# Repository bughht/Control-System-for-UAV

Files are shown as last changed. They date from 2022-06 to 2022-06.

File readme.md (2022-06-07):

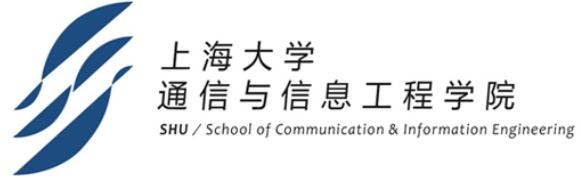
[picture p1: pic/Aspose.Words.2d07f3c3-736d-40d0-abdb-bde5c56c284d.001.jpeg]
scieyb


# 无人机自动投货系统

# **一、课题概述**

## **1.1 市场调研**

随着新科技被应用到如今的方方面面，企业和社会从中受益匪浅，当然，人们处理紧急情况的方式也变得多种多样。科技给我们带来了新的处理方式去处理紧急情况，为控制自然、人为等灾害的处置提供了新思路。随着美国联邦政府为无人机的运用出台的一些政策，无人机已经成为如今讨论的热点。和其他的科技一样，无人机的发展源自于军事应用。随着多轴无人机的发展，编程、稳定性、动力和价格方面都出现了改观，我们渐渐的也能制作出功能更复杂，功能更稳定的无人机。无人机处理紧急情况时拥有着令人关注的表现，给应急部门提供了一个新的思路来管理灾害的蔓延。

在过去，货物运送大多采用人工进行，这种模式无法高效快速地将所有小型货物准确的投掷到指定位置，对时间以及空间都有一定的限制，无法及时处理突发状况以及恶劣地形的跨越，也浪费人力资源。

2021年，中国民航局提出，在“十四五”期间，民航局将进一步扩大无人机物流配送试点范围。国家日益看重乡村振兴，大力发展乡村物流，无人机正成为推动乡村电商物流发展的重要利器。

结合现在科技的发展，我们需要找到让货物投掷便捷的方法来满足日益增长的需求。
## **1.2 需求分析**
（1）市场前景和应用价值

为了满足市场对无人机智能运输、准确投放上的需求，我们希望实现一个可便捷交互的基于树莓派和TM4C123GH6PM飞控板的无人机自动投弹系统。使用者可以通过拨码开关调整投掷物资的顺序，在飞机起飞之后，便可自动完成对周围场景的建模，寻找投放位置，躲避障碍并降落至投放区域，通过舵机自动投放，所有货物投放完成后自动返航等功能。以达到精准投放、自动返航的目的。

该项目的应用具有广泛性，可以用于各种无人投放场景，如偏远地区快递运送、极端地形物资投放等。且只需要一个激光雷达、一个摄像头、三个舵机、两块树莓派即可，性价比较高，可在多种地形上进行操作，通过拨码开关调整飞行程序，友好人性化，使用便捷。

（2）功能和核心技术

为了建立一个便捷、高效的无人机投放系统，我们主要实现三个功能：在指定位置投弹；路线规划和避障；稳定起飞和自动返航。

在指定位置投弹利用底部摄像头以及舵机，完成对无人机落地范围的控制。方便无人机及时地了解把握当前位置是否为投放位置；同时在画面上显示出投放位置的中心点和画面的中心点，方便程序实现期间的调试；根据计算可以得到无人机飞行方向，飞行距离。

路线规划和避障功能利用激光雷达对场景进行扫描的功能，获取障碍物所在的位置，由位置信息确定无人机飞行的路线。 

稳定起飞和自动返航功能，主要通过飞控板，控制螺旋桨调整飞行姿态和位置，并保持稳定。
## **1.3 实施过程**
（1）方案调整

①转接板PCB设计：计划初期我们原本打算用插针完成树莓派与舵机的连接，但因为连接不牢靠，更改为接线端子连接。由于我们的板子为异形板，设计空间较小，原定使用i2c等通信接口控制舵机等板载资源，但在实际过程中发现会导致树莓派性能降低，所以全部换为了普通GIOP口。

②树莓派与T265通信：为了压缩成本，我组打算用一块树莓派4b完成树莓派与T265等模块的通信。但在实验过程中发现，T265与树莓派4b的兼容性存在一定问题，连接不稳定，与老师讨论后认为是由树莓派USB硬件bug导致，因此，不得已再加入一块树莓派3b+，完成树莓派与T265的通信。

（2）具体进程

**A、实施阶段**

①初期学习、探索阶段

完成市场调研并进行分工，学习各自负责部分的相关内容，初步确定实施方案并进行试验测试可行性，了解树莓派与飞控板的通信方法。

第一周：确定课题，完成分工，完成市场调研。

第二周：详细计划完成，可行性报告完成。

第三周：树莓派环境配置，安装相应软件，学习相应知识。

第四周：学习3D打印，讨论无人机结构、投弹装置与电池仓设计。

②功能实现、制作阶段

完成PCB板以及3D打印部分，实现系统基础功能。

第三周：运用Altium Designer 完成PCB板设计。

第四周：PCB板送给厂家制作；树莓派与T265通信测试；

3D打印完成图纸设计；用3D打印得到的零件和实验室提供的零件尝试组装，试验无人机框架的结构。

第五周：PCB板完成焊接，LED灯模块、蜂鸣器模块调试；实现树莓派底部摄像头的部分功能；舵机功能测试；3D打印完成固定件。

第六周：实现舵机与树莓派的连接；实现树莓派程序对舵机的控制；树莓派激光雷达，T265的通信；3D打印外壳和支架等打印完成，底座设计完成；无人机各个模块的布局和应用设计。

第七周：3D打印基本完成；PCB板调试完成；各模块与树莓派数据包传输、舵机转动控制投放功能都已完成。

第八周：3D打印外壳优化完成；舵机供电改为5V电源供电；飞控板PID算法调试完成，可以实现起飞；飞控板与树莓派通信测试，经调整后可以正常工作；底部摄像头识别代码编写，基础功能可以实现。

③联合调试、完善阶段

飞控板与树莓派联合调试，可以实现基本功能。

第九、十周：各个模块代码整合；飞控板与树莓派通信；无人机联合调试，撰写结题报告。

2. **遇到的问题和解决方案**
1. 为了压缩成本，我组打算用一块树莓派4b完成树莓派与T265等模块的通信。但在实验过程中发现，T265与树莓派4b的通信存在问题，经常会断开连接，与老师讨论后认为是由树莓派USB口bug导致。再加入一块树莓派3b+后，问题解决。
1. 立创 EDA 绘制的 PCB 板文件不具有通用性，PCB 板重新使用 Altium Designer 设计。
1. 原来实验室中的机架无法完成项目要求，因此需要重新打印部分零件，以适配该任务。
1. 数字舵机与模拟舵机原理有些许不同，驱动代码有区别，需要修改，查阅资料调试后成功控制数字舵机。
1. 树莓派与无人机通信方面进展较缓慢，与组内成员项目互联通信时出现问题。检查后发现是树莓派转接板引脚虚焊导致，重新焊接后问题解决。
1. PCB 板排针与舵机杜邦线连接不牢固，同时舵机电源使用3.3V供电，电压不够，重新焊接改用5V 电源，取消杜邦线，连接就稳定了。
1. 飞机起飞时会向一侧偏离，飞控代码出现bug，查找修改后解决。

本小组成员在每次组会之后对存在的问题进行讨论，共同寻找解决方案，思路更加清晰、解决问题更加迅速。按照进度调整分工，让大家都有事可做，也提高了效率。

# **二、课题实施方案**
## **2.1 硬件总体方案**
小组成员根据本课题需完成的功能指标提出设计方案，并对可行性报告中最后确定的方案及课题实施中修改的方案进行说明，得出最后的最佳方案。

本项目的目标为制作一个自动无人机投弹系统，能够实时根据所处环境建立三维模型，根据三维模型规划路线，并完成投弹任务等。这需要我们设计并使用飞控板和树莓派开发板来进行数据分析和处理。基于以上需求，我们选择激光雷达作为我们测距建模的工具。讨论过后决定利用树莓派控制舵机进行投弹。使用TM4C123GH6PM飞控板控制飞行姿态。课题中树莓派需要实现较多功能，编写代码具有难度，在整个投弹系统中，需要较多的软件编写，实现课题目标。

本系统主要由四旋翼自主飞行器各部件构成。飞行器除机架、飞控板之外，主要包括激光雷达RPLIDAR A2和外接的树莓派及摄像头。下面分别论证整体设计方案中这几个模块的选择；首先，要完成定点投弹的功能，需要有较为准确的坐标系以保存所需遍历的点位信息。与用陀螺仪定位相比，T265所具有的精确坐标系更能体现出飞机的实时位置，也可以显著降低定位误差，故选用其坐标系统进行定位移动。其次，要实时判断飞行器下方是否为投弹区域，需要对无人机底部进行图像采集与图像处理。在本题中我们使用树莓派连接小型摄像头，采集底部中心一定范围之内的像素，并根据它们的色值判断其是否属于投弹区域。最后，在飞行到预定点位时，通过树莓派发出投弹指令。

本组采用的避障方式是使用SLAMTECA2激光雷达直接给出固定障碍物位置信息。因为激光雷达的精度更高，让无人机能够更好的检测当前处在的位置。故本组采用激光雷达对场景建模完成障碍物的识别。除此之外的基础功能包括舵机控制与 LED闪烁，蜂鸣器控制，都可以在树莓派上简便地完成。同时通过树莓派辅助处理飞行器速度信息。

基于总体设计方案，绘制的硬件原理框图如下图2.1。



图2.1  系统结构图
## **2.2 性能指标**
1. **飞行时间等：**起飞速度较快，垂直起飞，水平方向能按照预定路线稳定飞行。
1. **货物投掷位置与中心点距离：**底部摄像头能够准确的识别投放位置，并在相应的投放区域投放对应的货物，准确率较高。
1. **舵机控制：**舵机控制响应迅速，无多余抖动，水平旋转范围达 180°，能准确的放置货物仓中的货物并恢复原装。
1. **激光雷达：**能够通过激光雷达模块准确的建立模型，并且制定路线。
1. **稳定性：**在指定位置起飞后，能正常完成飞行认为并降落，偶尔会出现货物投放位置偏移。
## **2.3 开发平台**
无人机自动投弹系统开发采用的调试平台和软件编程语言。

1. PCB 板设计软件：Altium Designer。

`	`提供综合电子产品一体化开发所需的所有必须技术和功能。Altium Designer 在单一设计环境中集成板级和 FPGA 系统设计、基于 FPGA和分立处理器的嵌入式软件开发以及 PCB 版图设计、编辑和制造。并集成了现代设计数据管理功能,使得 Altium Designer 成为电子产品开发的完整解决方案——一个既满足当前，也满足未来开发需求的解决方案。

1. 3D 打印设计软件：Solidworks。

`	`Solidworks 是基于 Windows 平台的三维 CAD 设计和分析软件。其中 CAD 是计算机辅助设计（CAD-Computer Aided Design)是指运用计算机软件制作并模拟实物设计，展现新开发商品的外型、结构、彩色、质感等特色的过程。CAD 最早的应用是在汽车制造、航空航天以及大公司的电子工业生产中。之后随着CAD实现技术的演变和计算机价格的变化，其应用范围也逐渐变广，现广泛运用于平面印刷出版等诸多领域。

1. Keil MDK

`	`Keil MDK，也称MDK-ARM、Realview MDK、I-MDK、uVision4 等。Keil MDK是由三家[国内代理商]( )提供技术支持和相关服务。MDK-ARM软件为基于Cortex-M、Cortex-R4、ARM7、[ARM9处理器]( )设备提供了一个完整的开发环境。 MDK-ARM专为[微控制器](https://baike.baidu.com/item/%E5%BE%AE%E6%8E%A7%E5%88%B6%E5%99%A8/6688343)应用而设计，不仅易学易用，而且功能强大，能够满足大多数苛刻的嵌入式应用。

1. linux嵌入式操作系统

`	`Linux 内核最初只是由芬兰人林纳斯·托瓦兹（Linus Torvalds）在赫尔辛基大学上学时出于个人爱好而编写的。Linux 是一套免费使用和自由传播的类 Unix 操作系统，是一个基于 POSIX 和 UNIX 的多用户、多任务、支持多线程和多 CPU 的操作系统。Linux 能运行主要的 UNIX 工具软件、应用程序和网络协议。它支持 32 位和 64 位硬件。Linux 继承了 Unix 以网络为核心的设计思想，是一个性能稳定的多用户网络操作系统。
# **三、 课题实施详述**
## **3.1各模块设计**
1. PCB设计

`	`本项目需要用树莓派实现对舵机的控制，设计一块 PCB 板将树莓派 40 个引脚引出，针对需求对引脚进行合理的布局布线。PCB 板上设计了三个舵机插座、一个树莓派自身 5V电源插座、外部电源插座、蜂鸣器模块和 LED 模块，同时将剩余的引脚引到 PCB 板的上下端，以便备用，增加了 PCB 板的通用性。

①电路图设计思路

查阅树莓派引脚图资料，舵机的 PWM 波可由树莓派 GPIO 口直接输出，也可由特定的硬件 PWM 波 IO 口输出，将硬件 PWM 波 IO 口引出，（便可以测试两种方法，看哪个效果好就用哪一个）舵机还需要电源供电，考虑到用树莓派5V供电可能不够，便用转接板上的5V电源直接供电，并用MOS管驱动，树莓派控制的舵机在使用中能做到270°转动，但考虑到项目要求，一个舵机对软件编程会很困难，所以在 PCB 板上设计了三个舵机插座。引出树莓派自身 5V 供电电源，可以给一些小零件供电（比如风扇）。此外还设计了蜂鸣器模块和 LED 灯模块，蜂鸣器运用 MOS 管设计开关电路，GPIO 口输出高电平时，MOS 管导通，蜂鸣器响，反之，不响；LED 模块也是利用 GPIO 口输出PWM波控制MOS 管设计的开关电路，当输出高电平时，加上限流电阻，发光二极管便可以导通。

除了舵机、蜂鸣器等资源外，板子上还加入了一个5位拨码开关，降低编程同学的编程难度。

为了让树莓派更好的完成任务，我们在树莓派的CPU处加了小风扇进行主动散热，PCB设计的过程中，要避开风扇存在的区域。同时为了让转接板能稳定的安装在树莓派上，在板子四周留下过孔，便于对转接板固定。

电路原理图如下：



图 3.1 电路原理图

②各模块说明

LED 模块：GPIO 口输出高电平时，发光二极管导通，选择压降约为 0.7V 的发光二极管，MOS管压降约为0.3V，电源电压为 5V，发光二极管最大工作电流以 26mA 来计算，得限流电阻 R3=（5-0.7-0.3）/0.026 ≈150Ω，所以选择 150Ω 的电阻做为限流电阻，LED灯几乎达到最亮。

蜂鸣器模块：运用增强型NMOS管作开关，NMOS 的特性是Vgs大于一定的值就会导通，将 GPIO 输出口加到G极，当IO口输出高电平时大于限定值，MOS管导通，蜂鸣器发出声音。G极串联小电阻R1是为了减缓 Rds 从无穷大到 Rds(on)；防止电压突变 IO口与栅极电容形成 LC 震荡，串联电阻可以增大阻尼减小震荡效果；还能减小栅极充电峰值电流，一般取几欧姆到几十欧姆，这里选择 100Ω。栅极接地电阻 R2 是为了减少输入阻抗，减少对敏感信号的误动作，还有防静电的作用，阻值太大有可能起不到预期的效果，100kΩ 一般是比较可靠的。

舵机模块：GPIO 口输出高电平时，三极管导通，GPIO 口输出低电平时，三极管截止，因此在GPIO口输出PWM波时，MOS管源极处也能产生相应的PWM波，控制舵机旋转一定角度，然后复位。

插座模块：插座只需将需要的引脚连到同一个排针上即可。

最后将其余树莓派引脚引出即可。

③PCB 板的设计制作：

在画原理图之前，先将需要的所有元器件的封装找好，之后比较不容易出错，运用Altium Designer 画好原理图，打开封装管理器确保每个元器件封装尺寸，对应引脚正确，之后生成 PCB 设计图，进行布局和布线。在学习设计的过程中，要留意布局布线有各种规则（如电源线要比其他导线粗一些等），布局完成之前不要进行布线，否则，移动一个元件就会导致与它相连的线都必须重新连接。本项目的电路图较为简单，但板子面积较小，经过合理的布局之后正反两面的布线都没有出现交叉的情况。在布线完成后，对正反走线进行检查，添加丝印。在初步完成后，老师对 PCB 的设计提出了改进意见，首先连接外部电源的接线端子应该放在板子的边缘，方便插拔；其次 PCB 板与舵机的接口应该用接线端子，以提高连接的稳定性。最后是在板子上设计通孔（安装孔），方便以后系统增加功能需要叠加其他的板子，增加了 PCB 板的通用性。得到建议之后，再将 PCB 图进行修改布局布线，最后设置好各种规则，运行 DRC 检查，无误之后交给厂家生产。PCB 正反面图如下：



图 3.2 PCB正面



图 3.3 PCB 反面

拿到板子后，将元器件进行焊接，由于贴片电阻体积很小，焊接较为困难，在焊接的

过程中用万用表实时测试各个元件是否虚焊。在焊好第一个之后，联合舵机调试有问题，

于是重新焊接了一块板子，测试无误，PCB 板部分完成。

（2）舵机控制

树莓派 PWM 波输出端口控制舵机转动，用 GPIO23、24、25（实际地址）口进行软 PWM 波输出。运用库中的 PWM 函数控制数字舵机。用5V 电源供电。

舵机型号初选定为 TBSN-K15，通过树莓派 GPIO12 引脚输出硬件生成 PWM 波控角度。舵机的控制信号为周期是 20ms 的脉宽调制（PWM）信号，其中脉冲宽度从 0.5ms-2.5ms，相对应舵盘的位置为 0－180 度，呈线性变化，一一对应。也就是说，给它提供一定的脉宽，它的输出轴就会保持在一个相对应的角度上，无论外界转矩怎样改变，直到给它提供一个另外宽度的脉冲信号，它才会改变输出角度到新的对应的位置上。舵机内部有一个基准电路，产生周期 20ms，宽度 1.5ms 的基准信号，有一个比较器，将外加信号与基准信号相比较，判断出方向和大小，从而产生电机的转动信号。

舵机的控制电路板接受来自信号线的控制信号，控制电机转动，电机带动一系列齿轮组，减速后传动至输出舵盘。舵机的输出轴和位置反馈电位计是相连的，舵盘转动的同时，带动位置反馈电位计，电位计将输出一个电压信号到控制电路板，进行反馈，然后控制电路板根据所在位置决定电机的转动方向和速度，从而达到目标停止。

根据理论，只要输出占空比为 2.5%到 12.5%的 PWM 波信号，就可以控制舵机从0-180°旋转，但经过校准后，发现该数字舵机 0°是对应输出 5%的 PWM 波信号，180°对应 12.5%的 PWM 波信号，所以控制占空比在 5%-12.5%之间变化，转动角度也跟着线性变化。



图 3.4 舵机基本参数表和外观图

（3）树莓派

树莓派3B+系统结构图如下图6。

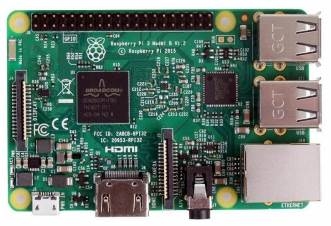
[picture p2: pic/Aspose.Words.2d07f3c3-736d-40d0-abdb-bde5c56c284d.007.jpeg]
src=http%3A%2F%2Fwww


图3.5树莓派系统结构图

树莓派3B+参数如下：

CPU型号：Broadcom BCM2837 芯片组，四核Cortex-A53（ARM v8）64位SoC @ 1.5GHz

内存： 8GB 

无线网卡： 2.4 GHz和5.0 GHz IEEE 802.11ac无线，蓝牙4.2，BLE

有线网卡： 1 x 10/100 以太网端口

USB接口： 4个USB 2.0端口

GPIO引脚： Raspberry Pi标准40针GPIO接头连接器（与以前的板完全向后兼容）

显示器接口： 1个micro-HDMI端口（最多支持4kp60）

DSI屏幕： 2通道MIPI DSI显示端口

CSI摄像头： 2通道MIPI CSI摄像机端口

视频输出： 4针立体声音频和复合视频端口

H.265（4kp60解码），H264（1080p60解码，1080p30编码）

OpenGL ES 3.0图形

内存卡插槽： Micro-SD卡插槽，用于加载操作系统和数据存储

电源输入： 通过USB-C连接器5V DC（最小3A \*）

通过GPIO接头提供5V DC（最小3A \*）

POE供电： 启用以太网供电（PoE）（需要单独的PoE HAT）

工作温度： 0 – 50摄氏度环境

4. 飞控板

如下图7所示。

PKRUR(A\_IE2F%Z91N8\_SANF 8SW2WH%OREE1HEN9[1WRD]4

图3.6 TM4C123GH6PM 飞控板

采用高性能的 TM4C123GH6PM 芯片，主频为 80MHz。电池电压经电调降压后输入飞控板，一路 3.3V 稳压负责供应板子上的核心芯片，另一路负责所有的外部设备。配备 2 路舵机接口，可以由飞控直接控制舵机转动。飞控板上从单片机引出了 1 路 I2C 接口和 4 路Uart 接口，具有丰富的扩展性。设计时为了使设备工作更加稳定，选用了 4 枚大容量钽电容，以应对电流陡升的情况，确保飞行稳定。

4. 激光雷达

RPLIDAR A2 由 SLAMTEC 公司开发的新一代低成本二维[激光](_blank)雷达(LIDAR)，它具有每秒高达 8000 次的高速激光测距采样能力。并配备了 SLAMTEC 独有的光磁融合(OPTMAG)专利技术，克服了传统激光雷达的寿命限制，可长时间可靠的稳定运行。

RPLIDAR A2 可以实现在二维平面的 12米半径范围内进行 360 度全方位的激光测距扫描，并产生所在空间的平面点云地图信息。这些云地图信息可用于地图测绘、机器人定位导航、物体/环境建模等实际应用中。本项目利用该雷达在飞行场地建立云图。

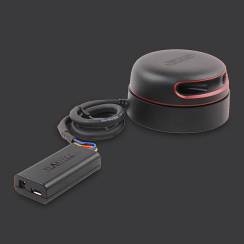
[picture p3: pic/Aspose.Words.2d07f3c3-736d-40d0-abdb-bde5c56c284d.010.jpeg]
o4YBAF3Of8WAKZXMAAC4QOJQnk8889


图3.7  RPLIDAR A2模块

（6）3D打印

`    `本产品使用SolidWork进行无人机的3D打印。打印的部件包括两块底板、树莓

派外挂板、三个投弹装置与八个机脚固定支架。

`    `底座板1提供与三个投弹装置的螺丝孔，提供超声底座连接的螺丝孔，同时

还提供与第二块底座板连接的减震球孔。如图9



图3.8 底座板

`    `第二块底板上有能够与第一块底座板连接的减震球孔，以及底部摄像头底座连接

的螺丝孔。如图10



图3.9 底座板2

`    `超声底座能够固定超声雷达，同时能够连接至底座板1。如图11



图3.10 超声底座

底部摄像头底座能够固定底部摄像头，同时能够连接至底座板2。如图12



图3.11 底部摄像头底座

投弹装置能够利用舵机装置来实现圆柱体的投放，固定在底座板1上。如图13



图3.12 投弹装置

树莓派外挂板提供树莓派以及树莓派扩展板的固定，侧板固定在无人机的底座

上。如图14



图3.13 树莓派外挂板

`    `机脚固定支架用于固定四个撑脚，使起飞与降落更加稳定。如图15



图3.14 机脚固定支架

`     `飞控底座上放置飞控模块，飞控底座通过减震球连接至中层板。如图16



图3.15 飞控底座

中层板提供与上层板的连接以及飞控底座的连接，最外侧提供与飞机主体的连

接。如图17



图3.16 中层板

`        `上层板提供激光雷达的支撑以及T260的支撑。如图18



图3.17 上层板

`    `飞机展示：

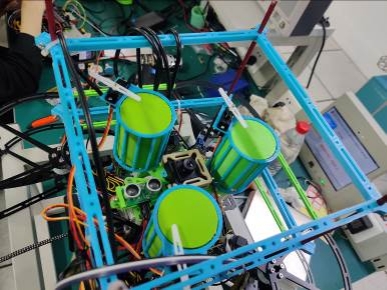
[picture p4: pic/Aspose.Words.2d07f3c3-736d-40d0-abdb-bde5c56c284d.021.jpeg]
DA1A3113C92C068D3B61A7594309E88E


图3.18 飞机底部

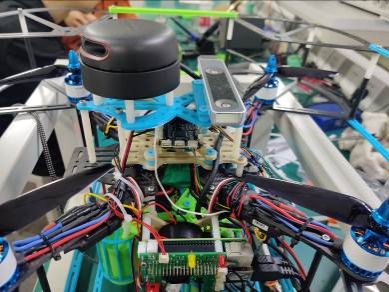
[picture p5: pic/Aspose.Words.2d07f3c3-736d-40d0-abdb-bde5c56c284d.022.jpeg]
288976D5343EC8E4D051DC27644402A7


图3.19 飞机顶部

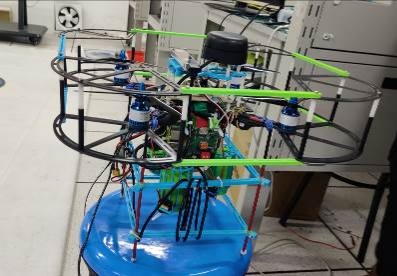
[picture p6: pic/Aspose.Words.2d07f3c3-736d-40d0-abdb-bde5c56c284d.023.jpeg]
AB2DF2DDD4166C45FAF4F75924F756BD


图3.20 飞机整体
## **3.2软件编程**
本飞机的基础框架基于408实验室的飞机，其基本的飞行功能早已成熟，因此在本报告中不再赘述。本章节后部分介绍的主要为本组在飞控上的改变以及为完成 本任务而新增的程序部分。

**（1）树莓派4b**

**①底部摄像头**

为了实现精准降落投货，我组在飞机的下部增加了一个对地摄像头。该摄像头和树莓派4b相连，主要用于抓取地面降落点中心的具体位置信息，再将信息通过自定义的编码方式，经由UART口传输到飞控程序中，辅助飞机落地。

具体实现过程：通过树莓派打开摄像头后，获取到其中的每帧图片信息，对得到的图片进行缩放、腐蚀以及膨胀等操作，得到一张便于处理的图片。由于地面降落区域中有大部分区域为红色，所以本组决定通过控制颜色阈值来找降落部分的中心。在得到对应颜色的RGB阈值之后，对处理过的图像进行mask处理，可以得到降落区域的范围图，再通过边缘检测，找到一个恰好框住降落区域最小的方形，该方形的中心即可粗略认为是降落区域的中心。流程图以及具体的算法流程如下图所示：



图3.21 底部摄像头算法流程

其中加入的降采样是为了减轻树莓派的计算负担，mask后的结构更易找到目标色块，根据边缘找中心点也可以稍微减轻计算量。进行以上优化后，树莓派可以实时处理视频图像。

为了改善程序对物理设备的状态控制，以面向对象的思想创建了一个Cam类。具体代码见附录。

**②激光雷达**

该任务中有避障这一环节，为解决这一问题，我组在飞机的最上方新增了一个激光雷达。该雷达也是和树莓派4b相连。在树莓派上安装好相关软件的驱动之后，就可以获得飞机四周的点图。之后确定滤除飞行区域外部的点，得到的就是飞行区域内的障碍物的点图，再根据极坐标的转换，就可以得到飞机内部坐标系下（即T265坐标系）障碍物的坐标。

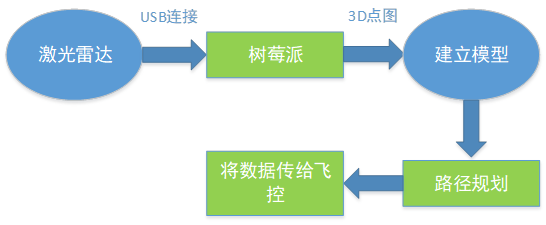
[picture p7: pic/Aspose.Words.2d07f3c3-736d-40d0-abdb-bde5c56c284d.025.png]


图3.22 激光雷达算法流程

路径规划：就是让检测到障碍物之后，以障碍物为圆心做圆，当飞机进入到以障碍物为圆心，一定范围内为半径的圆的边缘处时，就给予无人机一个对应圆环的切线的速度，使之能够走一个圆形避开障碍物。具体实现时，需要积累开始避障时圆形边缘的点和圆心的角度，到后面对应角度停止。示意图如下。

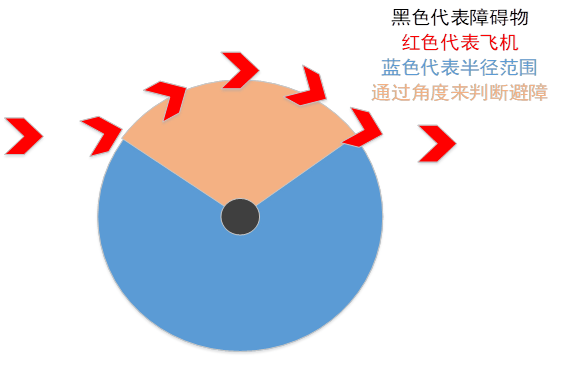
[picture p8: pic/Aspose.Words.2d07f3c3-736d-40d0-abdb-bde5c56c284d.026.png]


图3.23 飞机避障示意图

**③舵机控制**

当飞机成功降落到投货区域后，需要控制舵机将货物投下，为实现这一目标，我们将舵机和树莓派相连接，当树莓派接收到飞机发送过来的投货信号时，在对应的引脚上输出固定的PWM信号，控制舵机放下货物并且恢复原位。

为了方便调试，我们还在树莓派上加入了单独的蜂鸣器和LED灯（独立于飞控上的设备，方便通信方面的调试）。下为树莓派上引脚和接出来的硬件的对应图：

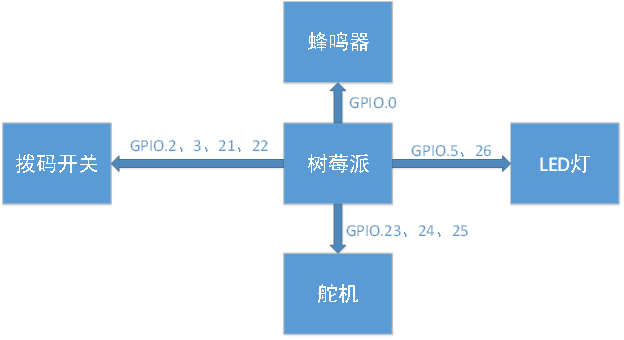
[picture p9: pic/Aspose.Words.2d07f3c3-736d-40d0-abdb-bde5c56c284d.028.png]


图3.24 树莓派与转接板连接引脚

由于这三个外接在树莓派上的设备都是用PWM驱动的，只是其中的脉宽以及占空比有一定打差距，下框图展示了树莓派如何在对应引脚上输出PWM信号。



图3.25 PWM波的输出

本次项目中，舵机、LED以及蜂鸣器的控制都是基于上图，但是为了用正确的PWM信号控制上述设备，中间所设计的参数有所不同。

驱动舵机需要不停地切换占空比，因此在程序设计时，我们用两个循环，设置两个渐变的占空比，实现自动打开舵机投货，并且在投货结束后自动关闭舱门。

LED灯和蜂鸣器的控制则轻松许多，只需要按照闪烁（鸣叫）的需求设置占空比即可。

1. 通信部分

原本我组想沿用之前的MAVLINK传输，但是由于其传输的性能在本飞机上并不佳，并且由于是祖传的代码，其中有一些问题难以通过代码简单解决，于是本组决定把部分通信协议改为基于UART口的hht协议。

重写的部分主要是树莓派4b和飞控之间的通信协议，我们将发送的数字压缩放入到一个数组中，通过UART口对进行二者之间的通信。该通信协议十分的简陋，仅有部分简单的对其和校验，但是经实验证明，已经可以满足我们的需求。前部分摄像头处理之后获得的图像信息、激光雷达处理后的障碍物的位置信息以及飞控给树莓派4b的投货信号都是通过这个协议进行传信的。

具体协议示意图如下：



图3.26 树莓派与飞控通信协议

1. 飞控部分的改进

为了进一步加快飞机飞行的速度，我们对飞控的部分代码进行了改写。

其一：我们对起飞进行了一定的优化，在飞机起飞之前加入了一段T265预载时间，这也可以大大减小T265在开机时出问题的可能性，再加上软件上的主动清零、校准，使得起飞时坐标系更加准确，有利于之后的定位。

其二：我们对基础的飞行代码也进行了一定的优化。之前的飞行是直接设置一个速度，用恒定速度进行飞行，最后用T265的数据进行校准，判断是否到位置。这样虽然可以完成飞行任务，但是飞行速度过慢，因此我们选择用速度控制实现直线飞行。与之前的恒定速度不同，新的控制代码用距离来控制速度，这样可以显著增加飞行速度，而且可以更好地找到重点。

其三：我们还将摄像头数据融入到飞控中，可以实现在直线上任意目标点停止（目标点有特殊标志）。

最后，我们还对降落进行了优化，为了节省时间，我们把原来的垂直下落改成倾斜下落，这样也能大幅度减少飞行时间，可以用更短的时间完成任务。
# **四、 系统测试及结果分析**
## **4.1 系统测试**
本项目的系统应用在 T408 实验室。烧录好程序后，用一个开关控制无人机开机，为实验室内师生提供极大便利，实物系统如下图。

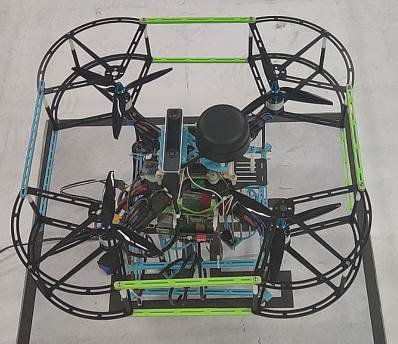
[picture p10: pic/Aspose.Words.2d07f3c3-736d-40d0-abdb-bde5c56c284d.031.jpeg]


图4.1 实物系统

在安装好电池并确认各个模块连接正常之后，便可开始本次测试。基于本项目的实质内容，将其主要分为三大模块：飞行寻路，躲避障碍和货物投掷。

1. 飞行寻路功能测试

①起飞稳定阶段

在起飞之前要先经过一段时间的准备和等待蜂鸣器鸣叫后，说明树莓派已经启动完备，准备起飞。如图4.2所示。

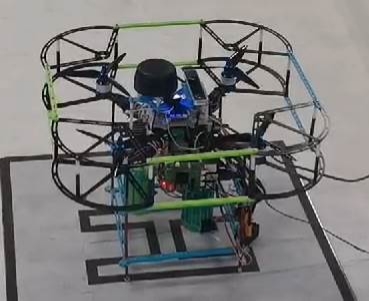
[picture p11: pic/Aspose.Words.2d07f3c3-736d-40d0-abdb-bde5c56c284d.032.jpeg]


图4.2 准备起飞阶段

起飞时，通过T265传回的数据调整飞行姿态，使飞机稳定起飞。定高飞行时如下图所示。

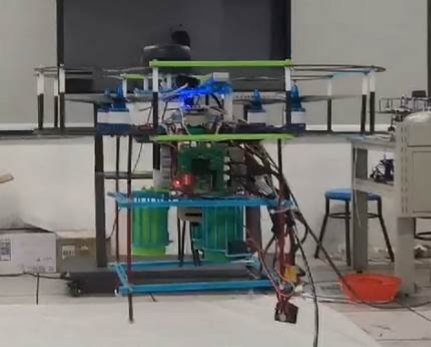
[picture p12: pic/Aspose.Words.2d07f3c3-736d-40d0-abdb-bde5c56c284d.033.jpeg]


图4.3 飞行定高阶段

起飞所花费时间如下表：

表4.1 飞行时间统计

|起飞测试次数|起飞消耗时间|
| :- | - |
|第一次测试|3.32s|
|第二次测试|3.45s|
|第三次测试|3.28s|
成功起飞后，向前飞行寻找投掷位置，并降落。

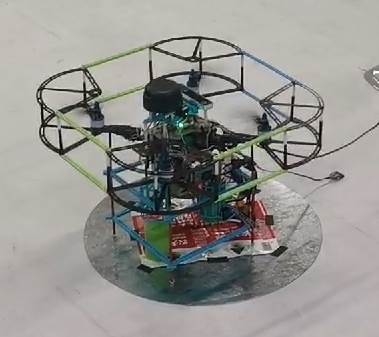
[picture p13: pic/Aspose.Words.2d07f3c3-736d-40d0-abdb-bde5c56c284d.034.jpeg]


图4.4	第一个点位降落位置

在找到第一个点位并降落后，树莓派控制舵机进行投弹，完成后再次起飞，向右侧飞行寻找第二个投弹位置。重复这一步骤，寻找第三个点位。

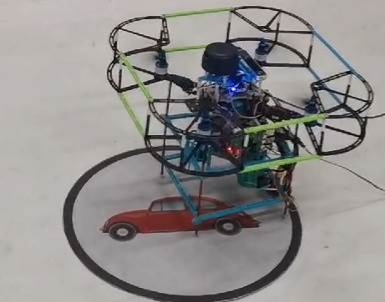
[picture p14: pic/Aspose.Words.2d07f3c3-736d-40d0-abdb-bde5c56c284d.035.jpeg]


图4.5	第二个点位降落位置

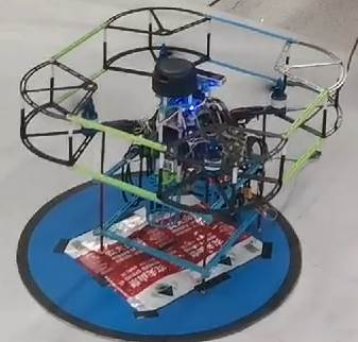
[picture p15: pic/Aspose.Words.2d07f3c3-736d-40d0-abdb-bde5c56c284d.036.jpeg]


图4.6	第三个点位降落位置

寻找完全部点位后，飞回起飞位置，并降落。降落位置如图4.7 所示。

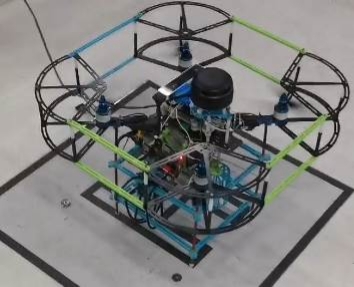
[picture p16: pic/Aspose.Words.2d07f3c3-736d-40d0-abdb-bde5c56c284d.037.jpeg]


图4.7 飞回起点的降落位置

1. 躲避障碍功能测试

在飞行的路上会人为设置障碍物，树莓派通过激光雷达建立返回的数据建立模型，并躲避障碍物，绕杆飞行躲避障碍时图片如下。

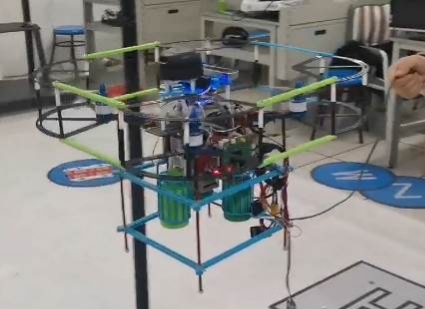
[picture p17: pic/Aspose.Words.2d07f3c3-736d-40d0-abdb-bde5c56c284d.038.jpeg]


图4.8 无人机避障

（3）货物投掷功能测试

当飞机成功降落到投货区域后，需要控制舵机将货物投下，为实现这一目标，我们将舵机和树莓派相连接，当树莓派接收到飞机发送过来的投货信号时，在对应的引脚上输出固定的PWM信号，控制舵机放下货物并且恢复原位。投掷位置如下图。



图4.9 第一个货物投掷位置



图4.10 第二个货物投掷位置

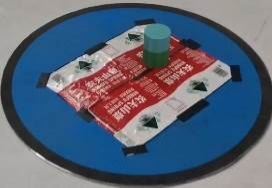
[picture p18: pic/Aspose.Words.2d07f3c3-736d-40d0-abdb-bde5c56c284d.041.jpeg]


图4.11 第三个货物投掷位置

调试飞控时有用到JLINK，以及串口助手。JLINK主要用于烧录飞控程序，在必要的时候还可以用它来调试部分飞控程序。串口助手则主要用于调试串口通信。等飞机起飞之后，我们就只能通过WiFi连接观察树莓派上的数据情况。

上面提到的所有新加的模块，我们都通过正确的手段进行测试过，保证每一个模块都可以完美运行之后才上电进行飞行测试。

最终在我们不懈的调试下，飞机可以成功完成全部的飞行任务。
## **4.2 结果分析**
以表格形式给出系统测试结果。

表4-2  系统测试结果

|**系统功能**|**设计结果**|**与设计指标间的偏差与分析**|
| :-: | :-: | - |
|**飞机起飞与寻路**|能够稳定起飞并且定高飞行，起飞时间较短，定高飞行时有微量偏移，可以忽略不计|无偏差，起飞流畅稳定。|
|**树莓派与飞控通信**|未起飞时通过串口测试，数据收发正常，起飞后也能正常通信，传输树莓派处理过的信息给飞控。|无偏差，能够根据数据及时调整飞行姿态。|
|**底部摄像头图像处理**|通过树莓派打开摄像头后，获取到其中的每帧图片信息，对得到的图片进行缩放、腐蚀以及膨胀等操作，得到一张便于处理的图片。再利用色彩阈值识别投弹位置，进行投掷。|有略微偏差，投掷位置与中心点相距5cm左右。|
|**激光雷达得到3D模型并规划路线避障**|在树莓派上安装好相关软件的驱动之后，就可以获得飞机四周的点图。之后确定滤除飞行区域外部的点，得到的就是飞行区域内的障碍物的点图，再根据极坐标的转换，就可以得到飞机内部坐标系下（即T265坐标系）障碍物的坐标。|无偏差，能够识别并躲避场地上的障碍。|
|**树莓派控制舵机投掷货物**|基于树莓派输出的 PWM 波实现了舵机的控制，初始化时 90 度，步进为 2度，可进行 0～180 以内任意角度的步进调整和定位调整。|无偏差，无人机可根据自身需求调整舵机释放货物|

# **五、总结与展望**
经过一个学期的努力，我们小组完成了无人机自动投弹系统这个项目。从项目初期的懵懂学习，到中期方案调整，最后到后期的功能完善，每一步我们都付出了很多心血。项目初期，我们进行了市场调研，了解到市场上各种无人机自动投弹系统的优缺点以及考虑到本身能力后，制定好了设计方案，最后得以实现系统基本功能。本课题可以实现对周围场景的建模，寻找投放位置，躲避障碍并降落至投放区域，通过舵机自动投放，所有货物投放完成后自动返航等功能。

通过这个项目，小组成员对 3D 打印、PCB 板设计、树莓派和飞控板都有了更多的了解，每个人对于自己的分内的工作都很上心，熟练掌握相关知识。在开发过程中，我们也遇到了许多问题，但我们每周都会进行小组研讨，对上周完成了任务做一个总结并讨论存在的问题，最终想出最佳的解决方案并尝试，这种探讨与思考不仅提高了我们解决问题的能力，还使得小组的凝聚力愈加深厚。

这个系统还有很大的改进空间，比如飞行器的结构并不完美，硬件资源潜力没有全部发挥等等，之后如果有机会，我们还会在系统上进行改进，对各种性能进行优化，使它成为一个更加完善和稳定的系统。
# **参考文献**
[1]Altium Designer2019四层板智能车PCB设计视频教程 https://b23.tv/2pwwB7

[2]赵宏、包广斌、马栋林.Python 网络编程(Linux)[M].清华大学出版社:北京,2018:16.

[3]陈鹏,李子卓,李陈龙,宋昊铭,吴心雨,迟英姿.物流无人机PID控制研究[J].无线互联科技,2021,18(23):112-113.

[4]芦竹茂,武娜,赵亚宁,白洋,韩钰,高海跃.基于激光雷达的无人机在杆塔附近的定位研究[J].激光与光电子学进展,2022,59(04):28-36.

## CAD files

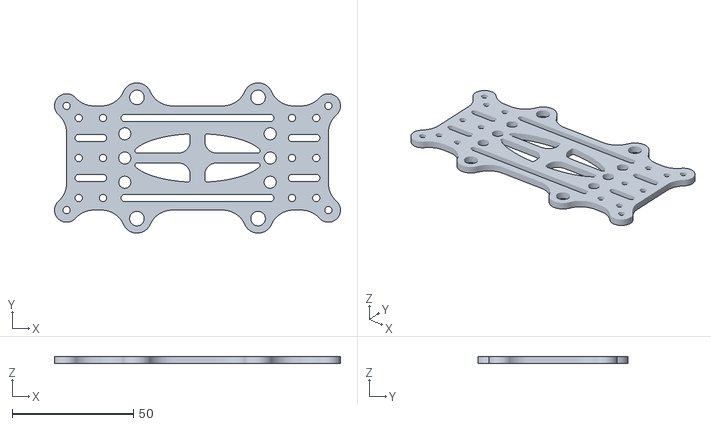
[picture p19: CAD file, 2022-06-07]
3D_Model/UP_BOTTOM v4.stl
118.0 x 62.0 x 3.00

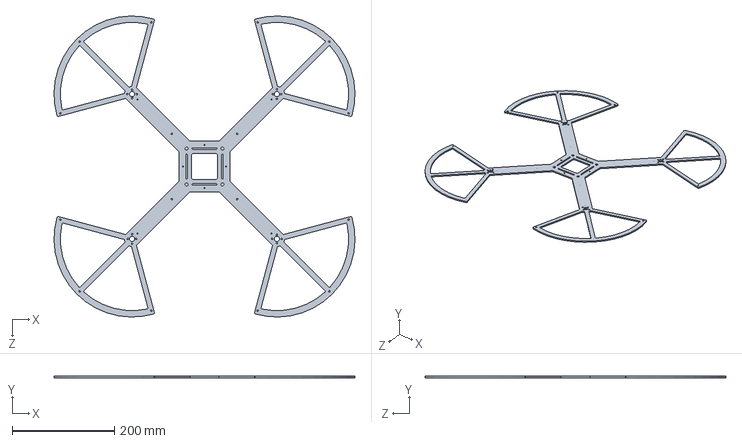
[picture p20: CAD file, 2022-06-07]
PCB/转接板 (3)/转接板/机架1.SLDPRT
587.8 x 3.00 x 587.8 mm

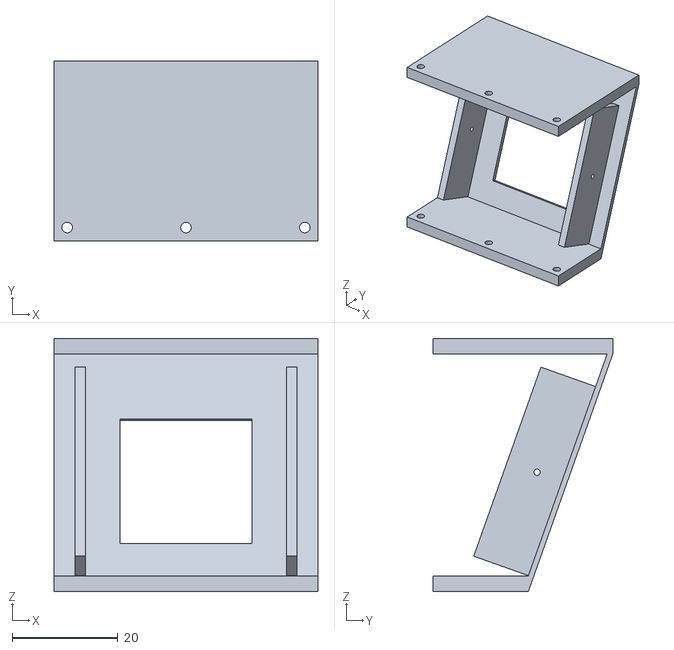
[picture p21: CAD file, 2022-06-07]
3D_Model/斜摄像头.STL
50.0 x 34.0 x 48.0

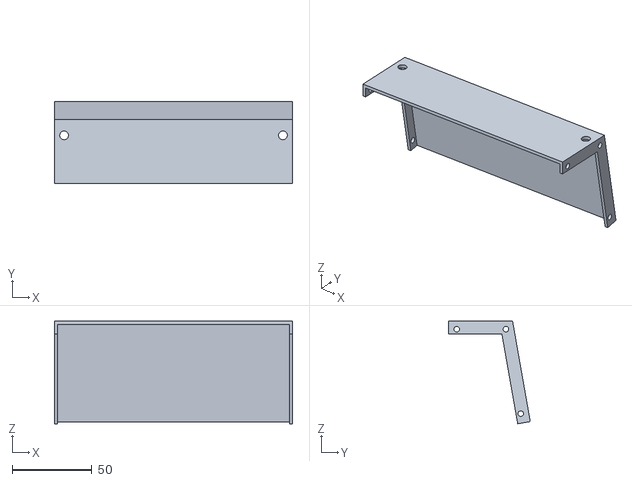
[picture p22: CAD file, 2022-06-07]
3D_Model/qian.STL
149.0 x 51.1 x 64.2

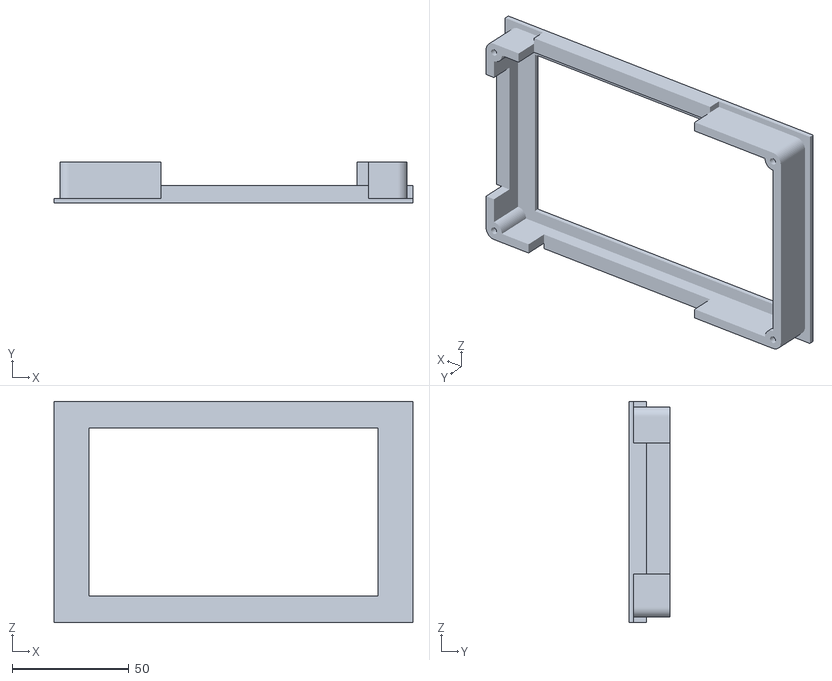
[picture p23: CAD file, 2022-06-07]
3D_Model/零件2.STL
154.0 x 17.6 x 95.0

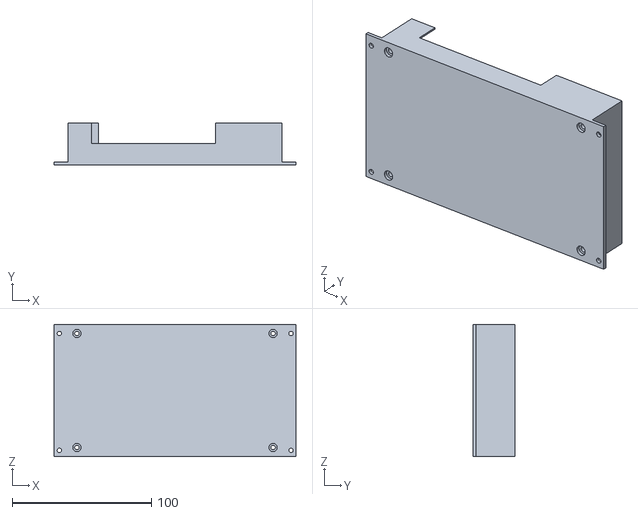
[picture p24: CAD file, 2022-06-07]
3D_Model/零件1.STL
174.0 x 30.0 x 95.0

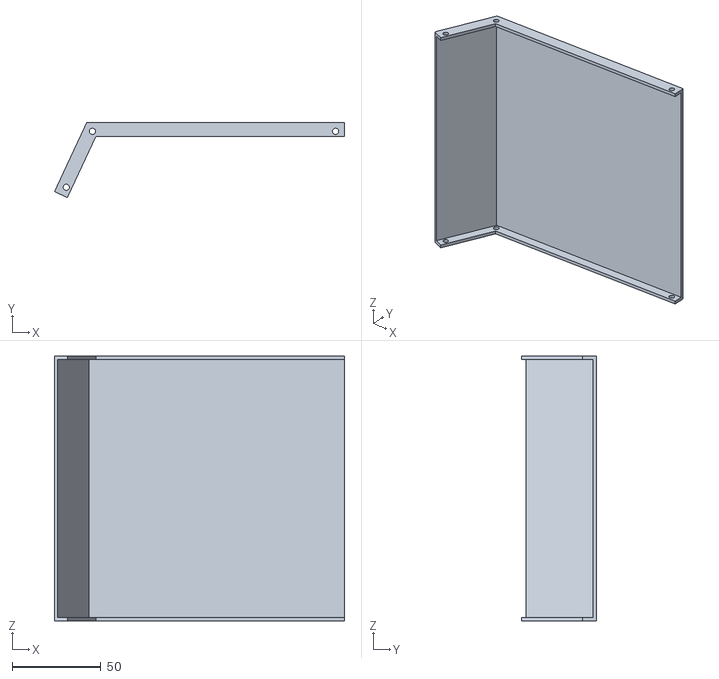
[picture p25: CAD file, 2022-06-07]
3D_Model/shang.STL
163.1 x 42.3 x 149.0

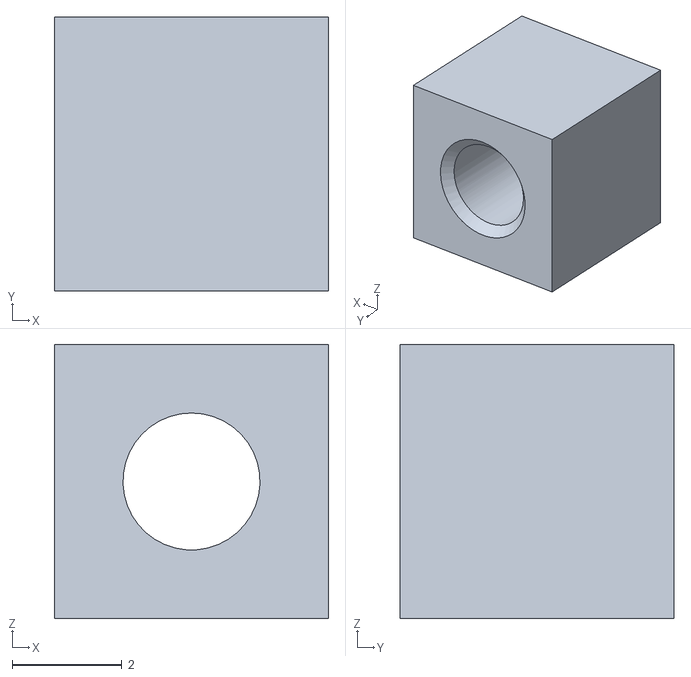
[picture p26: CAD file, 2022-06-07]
3D_Model/螺纹孔.STL
5.00 x 5.00 x 5.00

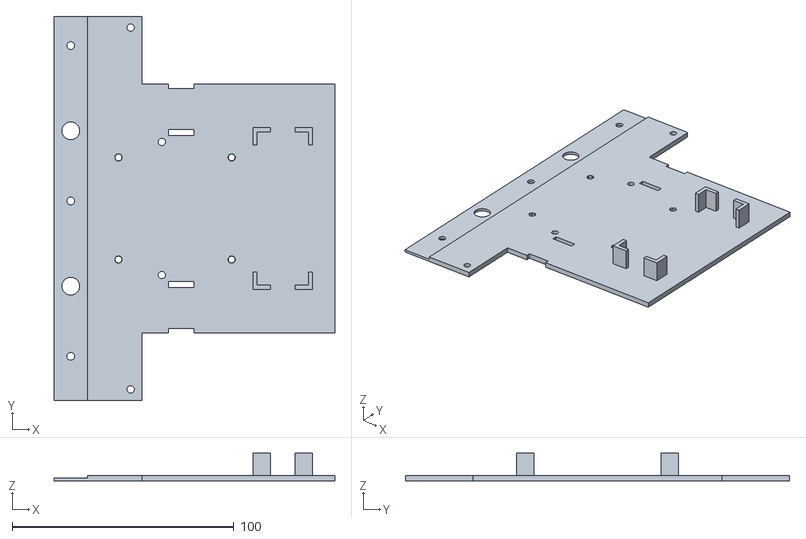
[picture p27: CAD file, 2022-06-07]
3D_Model/diban1-1.STL
126.5 x 173.0 x 12.5

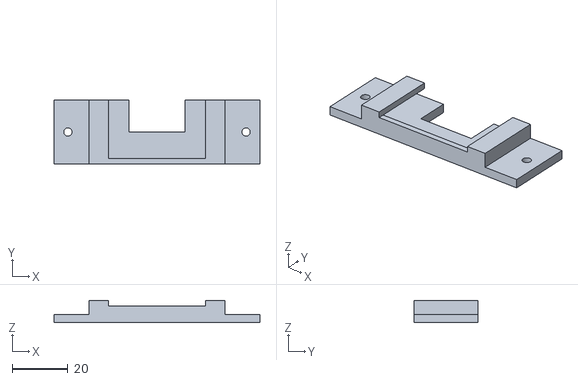
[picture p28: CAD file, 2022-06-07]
3D_Model/超声雷达.STL
74.0 x 23.0 x 8.00

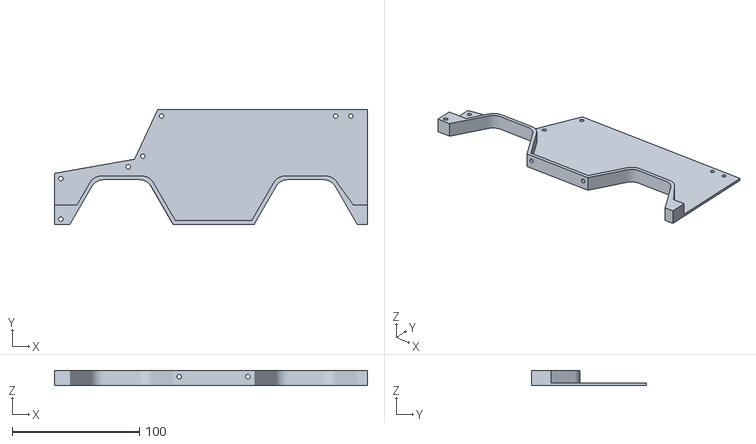
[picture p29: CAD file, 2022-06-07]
3D_Model/cemian1STL.STL
246.0 x 90.0 x 12.0

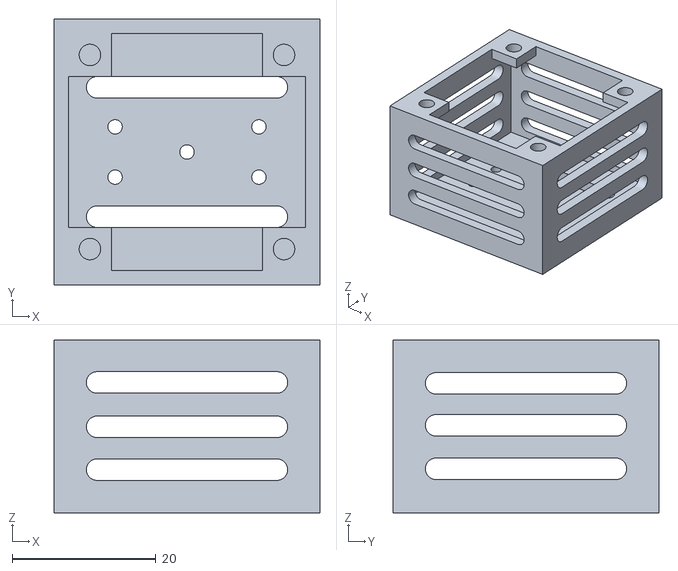
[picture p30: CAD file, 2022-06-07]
3D_Model/底部摄像头.STL
37.0 x 37.0 x 24.0

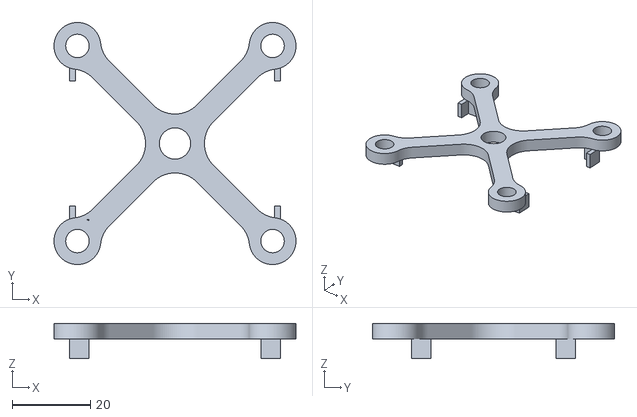
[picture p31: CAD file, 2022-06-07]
3D_Model/飞控.stl
62.0 x 62.0 x 9.00

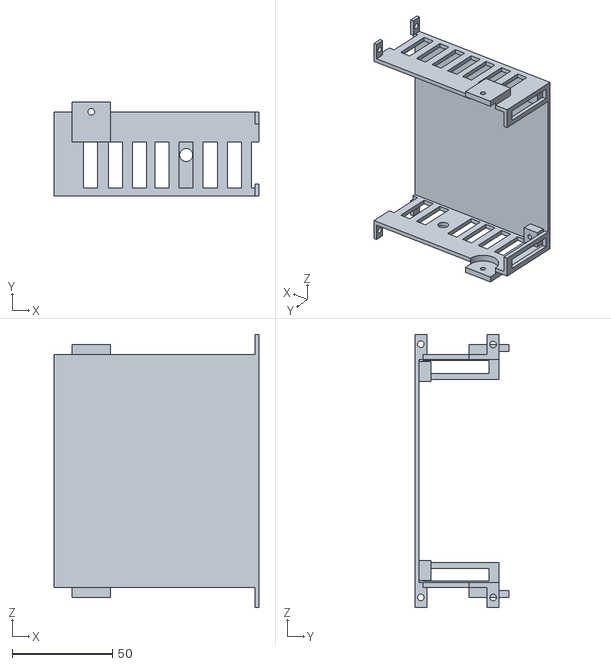
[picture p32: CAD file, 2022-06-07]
3D_Model/外壳1.3.1.STL
102.0 x 47.0 x 136.0

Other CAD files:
3D_Model/cemian2.STL
3D_Model/外壳1.3.2.STL
3D_Model/component2.STL
3D_Model/hou.STL
3D_Model/T265_BOTTOM.stl
3D_Model/cam_fast.stl
3D_Model/component1.STL
3D_Model/component3.STL
3D_Model/diban2.STL
3D_Model/圆柱1.STL

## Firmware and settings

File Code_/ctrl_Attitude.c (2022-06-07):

//朱文杰 20190101
//带模型ESO+反步姿态控制器
//悬停油门无参数观测器
//风力扰动观测器
//多旋翼优先级动力分配
//电机推力非线性修正
//论文正在发表
//！！请勿用于商业用途！！
//！！抄袭必究！！



#include "Basic.h"
#include "ctrl_Attitude.h"

#include "ControlSystem.h"
#include "MeasurementSystem.h"
#include "Configurations.h"
#include "drv_PWMOut.h"
#include "Receiver.h"
#include "Sensors.h"

#include "AC_Math.h"
#include "Quaternion.h"
#include "TD4.h"
#include "Filters_Butter.h"
#include "ESO_AngularRate.h"
#include "ESO_h.h"
extern vector3_float pos_vision;
extern float Height,Height_t265;
//extern int IsInTakeoff;
/*状态观测器*/
	//高度ESO
	static ESO_h ESO_height;
	static float hover_throttle = 0;
	static float WindDisturbance_x = 0;
	static float WindDisturbance_y = 0;
	static bool inFlight = false;
	
	static inline void update_output_throttle( float throttle , float h )
	{
		vector3_float AccENU = get_AccelerationCtrl();
		float output_minimum_throttle = Cfg_get_MotorStartingThrottle();
		float lean_cosin = get_lean_angle_cosin();
		
		//观测悬停油门
		float r_throttle = throttle - output_minimum_throttle;
		if( r_throttle < 0 )
			r_throttle = 0;
		r_throttle *= lean_cosin;
		ESO_h_update_u( &ESO_height , r_throttle );
		hover_throttle = ESO_h_run( &ESO_height , AccENU.z , h ) + output_minimum_throttle;
		
		//更新飞行状态
		static uint16_t onGround_counter = 0;
		if( inFlight == false )
		{
			onGround_counter = 0;
			if( AccENU.z > 20 && throttle > output_minimum_throttle + 5 )inFlight = true;
//			if (pos_vision.z > Height_t265+2)IsInTakeoff = 1;
//			if( pos_vision.z > Height_t265+10 && throttle > output_minimum_throttle + 5 ){inFlight = true;IsInTakeoff = -1;}
				
		}
		else
		{
			if( hover_throttle < output_minimum_throttle + 2 && \
					in_symmetry_range_float( AccENU.z  , 20 ) && \
					in_symmetry_range_float(  get_VelocityENU().z  , 25 ) \
			
//					in_symmetry_range_float( vector3_float_square( AccENU ) , 20*20 ) && \
//					in_symmetry_range_float( vector3_float_square( get_VelocityENU() ) , 25*25 ) \
					
				)
			{
				if( ++onGround_counter >= 300 )
					inFlight = false;
			}
			else
				onGround_counter = 0;
		}
		
		//观测水平分力
		if( inFlight )
		{
			vector3_float active_force_xy_vec = Quaternion_rotate_axis_z( get_history_Airframe_attitude( 0.42f / 10 ) );
			if( lean_cosin < 0.3f )
				lean_cosin = 0.3f;
			active_force_xy_vec = vector3_float_mult( active_force_xy_vec , ( AccENU.z + constG ) / lean_cosin );
			vector3_float WindDisturbance_xy;
			WindDisturbance_xy.x = AccENU.x - active_force_xy_vec.x;
			WindDisturbance_xy.y = AccENU.y - active_force_xy_vec.y;
			
			float lp_factor = 2 * PI_f * (1.0f/200) * 0.3f;
			WindDisturbance_x += lp_factor * ( WindDisturbance_xy.x - WindDisturbance_x );
			WindDisturbance_y += lp_factor * ( WindDisturbance_xy.y - WindDisturbance_y );
		}
		else
			WindDisturbance_x = WindDisturbance_y = 0;
	}
/*状态观测器*/
	
/*观测器*/
	float get_hover_throttle()
	{
		return hover_throttle;
	}
	bool get_is_inFlight()
	{
		return inFlight;
	}
	void set_inFlight_false(){
		inFlight = false;
	}
	float get_WindDisturbance_x()
	{
		return WindDisturbance_x;
	}
	float get_WindDisturbance_y()
	{
		return WindDisturbance_y;
	}
/*观测器*/

/*模式及期望*/
	//期望TD4滤波器
	static TD4 Target_tracker[3];
	//姿态ESO
	static ESO_AngularRate ESO[3];
	//扰动滤波器
	static Filter_Butter2_LP_float disturbance_filter[3];

	//姿态控制模式
	static bool Attitude_Control_Enabled = false;
	static Attitude_ControlMode RollPitch_ControlMode = Attitude_ControlMode_Angle;
	static Attitude_ControlMode Yaw_ControlMode = Attitude_ControlMode_Angle;
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

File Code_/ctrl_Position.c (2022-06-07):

#include "Basic.h"
#include "ctrl_Position.h"

#include "ControlSystem.h"
#include "MeasurementSystem.h"
#include "Configurations.h"
#include "drv_PWMOut.h"
#include "Receiver.h"
#include "Sensors.h"

#include "AC_Math.h"
#include "Quaternion.h"
#include "TD4.h"
#include "Filters_Butter.h"

/*模式及期望*/
static bool Altitude_Control_Enabled = false;
static bool Position_Control_Enabled = false;

//位置控制模式
static Position_ControlMode Altitude_ControlMode = Position_ControlMode_Position;
static Position_ControlMode HorizontalPosition_ControlMode = Position_ControlMode_Position;

//期望TD4滤波器
static TD4 Target_tracker[3];
//期望速度低通滤波器
static Filter_Butter4_LP_float TargetVelocityFilter[3];

static vector3_float target_position;
static vector3_float target_velocity;
static float VelCtrlMaxRoll = -1, VelCtrlMaxPitch = -1;

// glw 喇叭相关
extern int Buzzer_flag;

int Buzzer_flag = 0;

// glw 起飞相关
//	extern int IsInTakeoff;
//	int IsInTakeoff = 0;
extern vector3_float pos_vision;
extern float Height, Height_t265;
/*高度*/
bool Altitude_Control_Enable()
{
	if (Altitude_Control_Enabled == true ||
		get_Altitude_Measurement_System_Status() != Measurement_System_Status_Ready)
		return false;

	Altitude_ControlMode = Position_ControlMode_Locking;
	Altitude_Control_Enabled = true;
	Attitude_Control_Enable();
	return true;
}
bool Altitude_Control_Disable()
{
	if (Altitude_Control_Enabled == false)
		return false;
	Altitude_Control_Enabled = false;
	Position_Control_Disable();
	return true;
}

Position_ControlMode get_Altitude_ControlMode()
{
	return Altitude_ControlMode;
}

bool Position_Control_set_TargetPositionZ(float posz)
{
	if (Altitude_Control_Enabled == false)
		return false;
	target_position.z = posz;
	if (Is_PositionControlMode(Altitude_ControlMode) == false)
		Target_tracker[2].x1 = get_Position().z;
	Altitude_ControlMode = Position_ControlMode_RouteLine;
	return true;
}
bool Position_Control_set_TargetPositionZRelative(float posz)
{
	return Position_Control_set_TargetPositionZ(get_Position().z + posz);
}
bool Position_Control_set_TargetVelocityZ(float velz)
{
	if (Altitude_Control_Enabled == false)
		return false;
	target_velocity.z = velz;
	Altitude_ControlMode = Position_ControlMode_Velocity;
	return true;
}
bool Position_Control_set_ZLock()
{
	if (Altitude_Control_Enabled == false)
		return false;
	if (Altitude_ControlMode == Position_ControlMode_Velocity)
		Altitude_ControlMode = Position_ControlMode_Locking;
	return true;
}

//起飞到当前高度上方的height高度
static float TakeoffHeight;
bool Position_Control_Takeoff_HeightRelative(float height)
{
	if (Altitude_Control_Enabled == false)
		return false;
	if (height < 10)
		return false;
	if (get_is_inFlight() == true)
		return false;

	Altitude_ControlMode = Position_ControlMode_Takeoff;
	TakeoffHeight = height;
	return true;
}
/*高度*/

/*水平位置*/
bool get_Position_Control_Enabled()
{
	return Position_Control_Enabled;
}
bool Position_Control_Enable()
{
	if (Position_Control_Enabled == true ||
		get_Position_Measurement_System_Status() != Measurement_System_Status_Ready)
		return false;

	HorizontalPosition_ControlMode = Position_ControlMode_Locking;
	Position_Control_Enabled = true;
	Altitude_Control_Enable();
	return true;
}
bool Position_Control_Disable()
{
	if (Position_Control_Enabled == false)
		return false;
	Position_Control_Enabled = false;
	return true;
}

Position_ControlMode get_Position_ControlMode()
{
	return HorizontalPosition_ControlMode;
}

//直线方程系数
static float LineA, LineB, LineC, LineInvA2PB2;
bool Position_Control_set_TargetPositionXY(float posx, float posy)
{
	if (Position_Control_Enabled == false)
		return false;
	target_position.x = posx;
	target_position.y = posy;

	//求直线方程
	vector3_float current_pos = get_Position();
	LineA = current_pos.y - target_position.y;
	LineB = target_position.x - current_pos.x;
	LineC = current_pos.x * target_position.y - target_position.x * current_pos.y;
	float A2PB2 = LineA * LineA + LineB * LineB;

	if (A2PB2 > 1 * 1)
	{ //长距离进入巡线模式
		LineInvA2PB2 = 1.0f / A2PB2;
		HorizontalPosition_ControlMode = Position_ControlMode_RouteLine;
	}
	else //短距离进入位置锁定模式
		HorizontalPosition_ControlMode = Position_ControlMode_Position;
	return true;
}
bool Position_Control_move_PositionXYRelative(float posx, float posy)
{
	if (Position_Control_Enabled == false)
		return false;
	target_position.x += posx;
	target_position.y += posy;
	LineC -= LineA * posx + LineB * posy;
	return true;
}
bool Position_Control_set_TargetPositionXYRelative(float posx, float posy)
{
	vector3_float current_pos = get_Position();
	return Position_Control_set_TargetPositionXY(current_pos.x + posx, current_pos.y + posy);
}
bool Position_Control_set_TargetPositionXYRelativeBodyHeading(float posx, float posy)
{
	vector3_float current_pos = get_Position();
	float Yaw = Quaternion_getYaw(get_Airframe_attitude());
	float Yaw_sin, Yaw_cos;
	arm_sin_cos_f32(rad2degree(Yaw), &Yaw_sin, &Yaw_cos);
	float posx_ENU = map_BodyHeading2ENU_x(posx, posy, Yaw_sin, Yaw_cos);
	float posy_ENU = map_BodyHeading2ENU_y(posx, posy, Yaw_sin, Yaw_cos);
	return Position_Control_set_TargetPositionXY(current_pos.x + posx_ENU, current_pos.y + posy_ENU);
}
bool Position_Control_move_TargetPositionXYRelativeBodyHeading(float posx, float posy)
{
	float Yaw = Quaternion_getYaw(get_Airframe_attitude());
	float Yaw_sin, Yaw_cos;
	arm_sin_cos_f32(rad2degree(Yaw), &Yaw_sin, &Yaw_cos);
	float posx_ENU = map_BodyHeading2ENU_x(posx, posy, Yaw_sin, Yaw_cos);
	float posy_ENU = map_BodyHeading2ENU_y(posx, posy, Yaw_sin, Yaw_cos);
	return Position_Control_move_PositionXYRelative(posx_ENU, posy_ENU);
}
bool Position_Control_set_TargetPositionXY_LatLon(double Lat, double Lon)
{
	if (Position_Control_Enabled == false)
		return false;
	float x, y;
	if (get_Point_From_LatLon(&x, &y, Lat, Lon) == false)
		return false;
	return Position_Control_set_TargetPositionXY(x, y);
}

bool Position_Control_set_TargetVelocityBodyHeadingXY(float velx, float vely)
{
	if (Position_Control_Enabled == false)
		return false;

	//将速度旋转至ENU
	float Yaw = Quaternion_getYaw(get_Airframe_attitude());
	float Yaw_sin, Yaw_cos;
	arm_sin_cos_f32(rad2degree(Yaw), &Yaw_sin, &Yaw_cos);
	float velx_ENU = map_BodyHeading2ENU_x(velx, vely, Yaw_sin, Yaw_cos);
	float vely_ENU = map_BodyHeading2ENU_y(velx, vely, Yaw_sin, Yaw_cos);

	target_velocity.x = velx_ENU;
	target_velocity.y = vely_ENU;
	HorizontalPosition_ControlMode = Position_ControlMode_Velocity;
	VelCtrlMaxRoll = VelCtrlMaxPitch = -1;
	return true;
}
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
